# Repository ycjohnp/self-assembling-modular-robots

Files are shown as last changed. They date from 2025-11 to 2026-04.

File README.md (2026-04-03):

# A Fully Automatic Self-Assembling Modular Robot System (Archived)



 This project showcases the design and manufacturing of a self-assembling modular robotic system, with each robot possessing 4 degrees of freedom, wheel-based locomotion, Bluetooth and Wi-Fi capabilities, and an electromagnet-based connection system.

Controlled through a combination of AprilTags, computer vision using OpenCV, and PID controllers for precise position and movement instructions, the system's functionality has been validated through extensive tests. These tests include assessing the robot's speed in various assembly configurations, speed under cargo load, and the strength of inter-robot connections. Simulated challenging environments were created to validate the overall self-assembly performance of the robotic system.

## How This Project Started

During the spring of 2022, Shanghai went into a 3-month long lockdown, due to a major Covid-19 outbreak. During that time we were unable to leave our homes and for many weeks we had a hard time getting supplies and food or getting anything delivered since essential logistics and delivery workers were unable to go to work. 

During that time I started researching: "How can we increase the reliability of logistics and delivery networks?" Many of the ideas that popped up during that initial research mentioned **flexibility** and **adaptability** in the industry and in the subprocess (eg. last-mile delivery, warehousing, transportation, etc.).

Going off of my past robotics experience, I knew that modular robots met the exact characteristics mentioned above. Seeing current modular robotics research focused on search & rescue and static applications of modular robots (such as sending them to Mars before humans to build structures), I wondered: "Can we use robots that solve challenges together to increase reliability and decrease human dependence of logistics systems?”

I began this project to build a self-assembling modular robot system for logistics, though its design can be applied to other use cases as well. Although this is just a proof-of-concept system, I hope the insights from this research can open up possibilities for further industrial applications of modular robotics. By doing so, I hope that this critical part of our daily lives becomes more resilient against extreme situations
## Demo
Modular Robot Demo (http://www.youtube.com/watch?v=8HDp2pXij3Y "Modular Robot Demo")

## Project Pictures





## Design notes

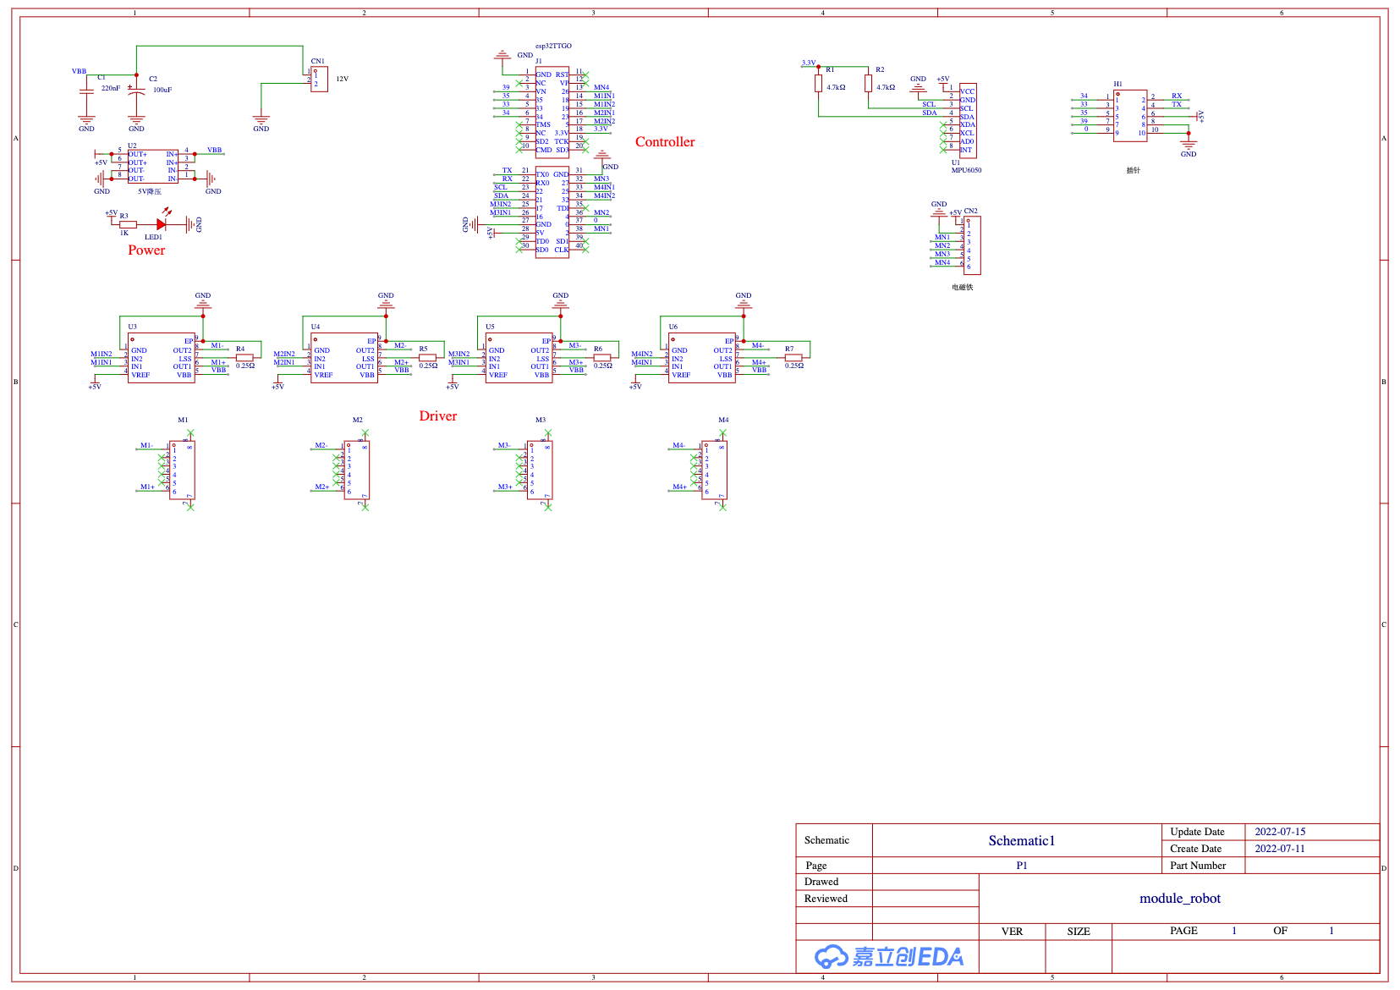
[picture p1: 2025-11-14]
Extension Board PCB/PCB Schematics.png

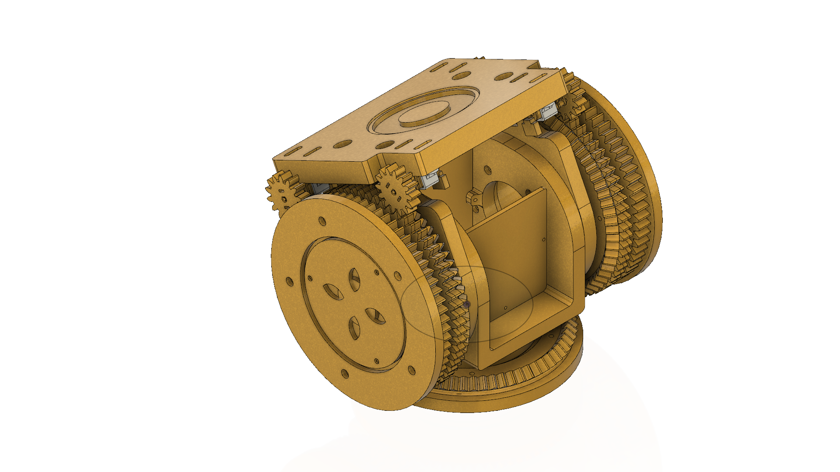
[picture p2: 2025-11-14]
3D Files/Module_robot.png

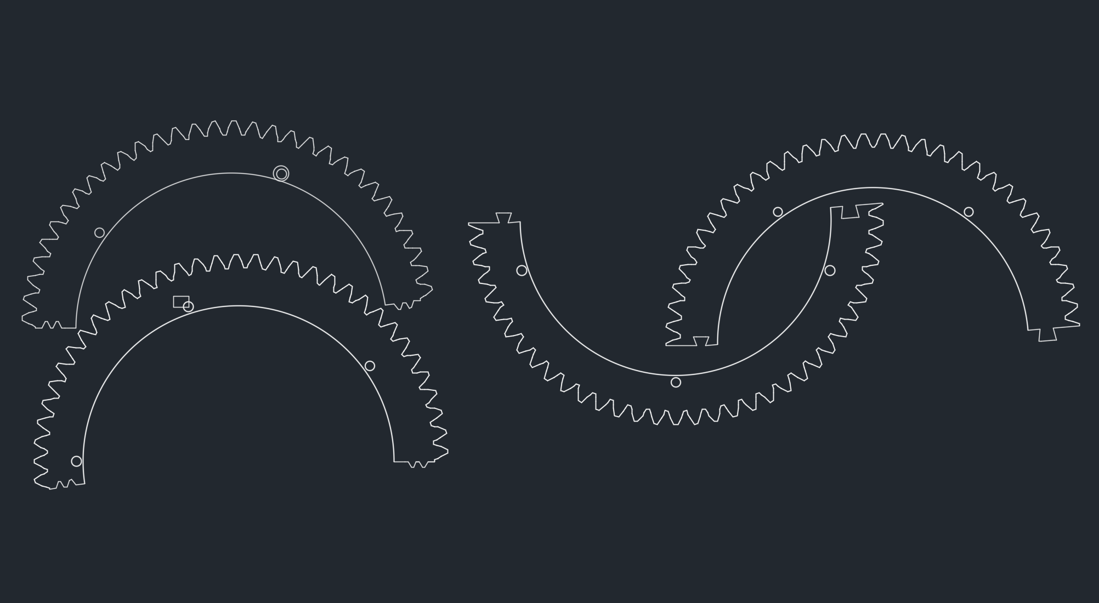
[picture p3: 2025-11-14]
2D DWG/Bevel Gear Halves DWG.png

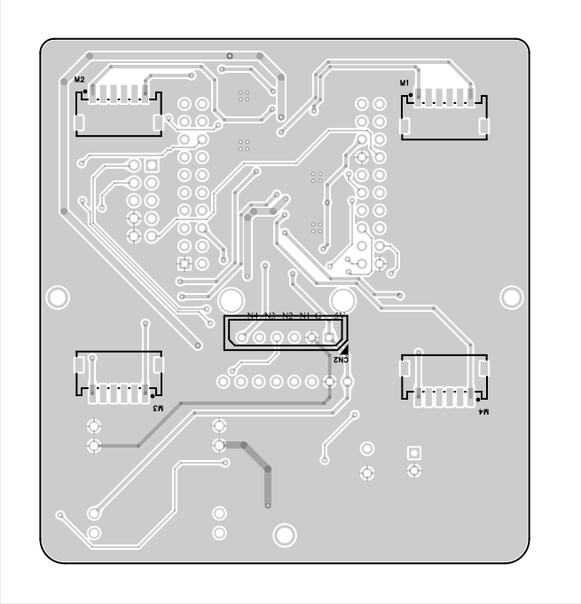
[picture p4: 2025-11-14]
Extension Board PCB/PCB Back.png

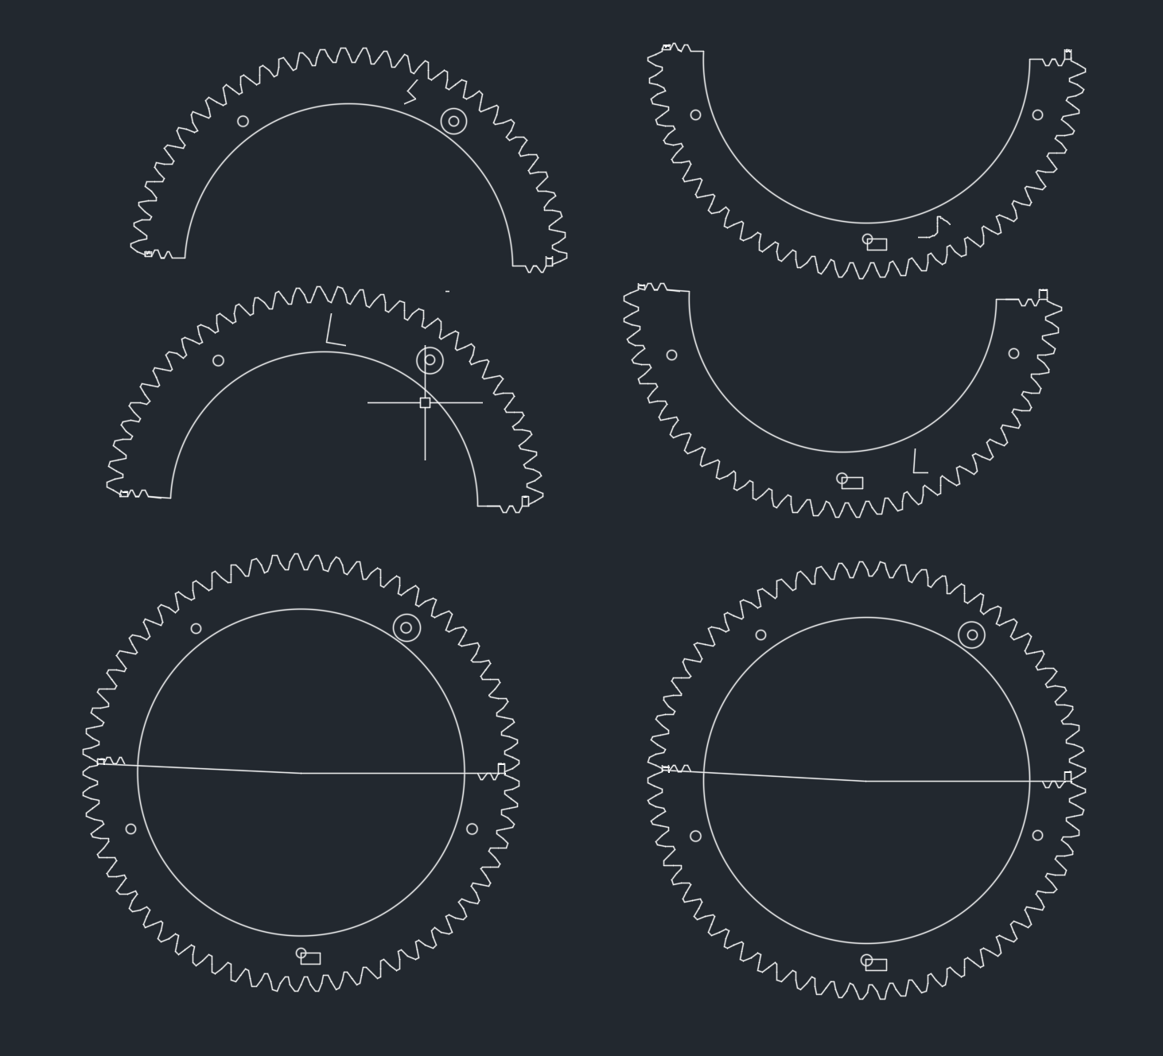
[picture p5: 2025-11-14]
2D DWG/Wheel Gear Halves DWG.png

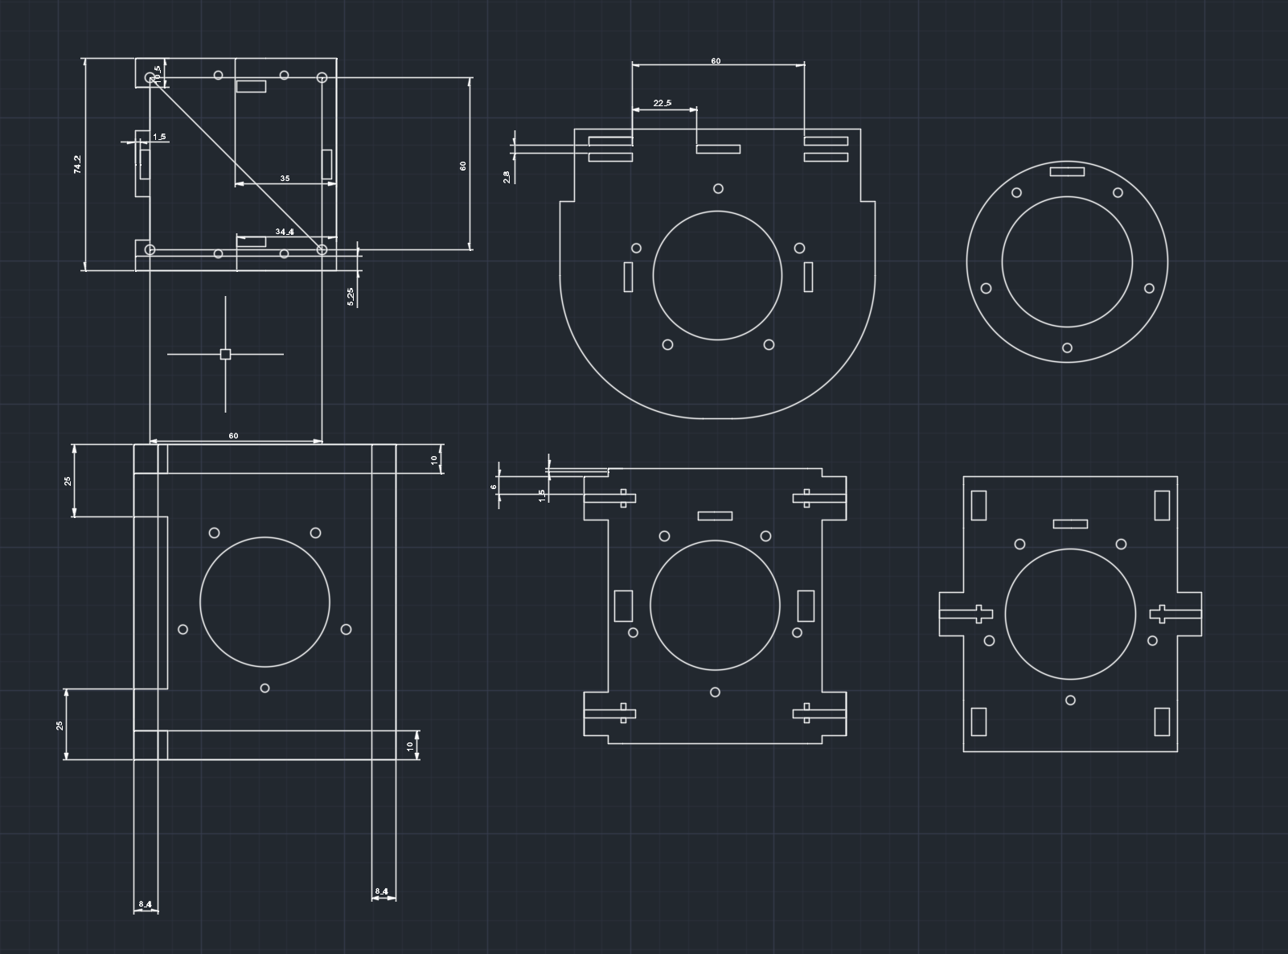
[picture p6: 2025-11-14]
2D DWG/Center Frame DWG.png

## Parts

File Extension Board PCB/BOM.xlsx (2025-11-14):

No. | Quantity | Device | Designator | Footprint | Value | Manufacturer Part | Manufacturer | Supplier Part | Supplier
1 | 1 | TCC0603X5R224M250CT | C1 | C0603 | 220nF | TCC0603X5R224M250CT | CCTC(三环) | C713508 | LCSC
2 | 1 | RG050M101LO8*12TA-1A1E | C2 | CAP-TH_BD8.0-P3.50-D0.6-FD | 100uF | RG050M101LO8*12TA-1A1E | BERYL(绿宝石) | C357618 | LCSC
3 | 1 | HC-5264-2A | CN1 | CONN-TH_2P-P2.50_HCTL_HC-5264-2A |  | HC-5264-2A | HCTL(华灿天禄) | C2845814 | LCSC
4 | 1 | HC-5264-6A | CN2 | CONN-TH_6P-P2.50_HCTL_HC-5264-6A |  | HC-5264-6A | HCTL(华灿天禄) | C2845818 | LCSC
5 | 1 | HDR-M_2.54_2x5 | H1 | HDR-TH_10P-P2.54-V-M-R2-C5-S2.54 |  |  |  | C124387
6 | 1 | esp32ttgo | J1 | esp32TTGO
7 | 1 | LED_0603-R | LED1 | LED0603-RD_BLUE |  |  |  | C72044
8 | 4 | KH-ZH1.5WF-06A | M1,M2,M3,M4 | CONN-SMD_KH-ZH1.5WF-06A |  | KH-ZH1.5WF-06A | kinghelm(金航标) | C2688783 | LCSC
9 | 2 | AR05DTCW1002 | R1,R2 | R0805 | 4.7kΩ | AR05DTCW1002 | 光颉(Viking) | C319941 | LCSC
10 | 1 | Res_0603 | R3 | R0603 | 1K
11 | 4 | CR2512FR250E04R | R4,R5,R6,R7 | R2512 | 0.25Ω | CR2512FR250E04R | EVER OHMS(天二科技) | C147045 | LCSC
12 | 1 | MPU6050 | U1 | MPU6050
13 | 1 | bianyaqi | U2 | bianyaqi
14 | 4 | A4950ELJTR-T | U3,U4,U5,U6 | SOIC-8_L4.9-W3.9-P1.27-LS6.0-BL-EP |  | A4950ELJTR-T | ALLEGRO(美国埃戈罗) | C82404 | LCSC

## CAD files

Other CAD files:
2D DWG/Bevel Gear Halves DWG.dwg
2D DWG/Wheel Gear Halves DWG.dwg
2D DWG/Center Frame DWG.dwg

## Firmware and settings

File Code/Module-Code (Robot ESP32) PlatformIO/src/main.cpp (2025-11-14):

#include <Arduino.h>
#include "ESPMotor.hpp"
#include <MPU6050_tockn.h>
#include <Wire.h>
#include <esp_now.h>
#include <WiFi.h>

typedef struct test_struct
{
  float distance; // x
  float angle;    // y
  float state;    // z
} test_struct;

test_struct myData;

void OnDataRecv(const uint8_t *mac, const uint8_t *incomingData, int len)
{
  memcpy(&myData, incomingData, sizeof(myData));
  // Serial.print("Bytes received: ");
  // Serial.println(len);
  // Serial.print("x: ");
  Serial.print(myData.distance);
  Serial.print(",");
  Serial.print(myData.angle);
  Serial.print(",");
  Serial.print(myData.state);
  Serial.println();
}

// PWM availible on : 2, 4, 5, 12 - 19, 21 - 23, 25 - 27, 32 - 33
//----------------------------------------------------------------
// Motor Pins
#define M1IN1 18
#define M1IN2 19
#define M2IN1 23
#define M2IN2 5
#define M3IN1 16
#define M3IN2 17
#define M4IN1 25
#define M4IN2 32
//----------------------------------------------------------------
// Electromagnet Pins
#define magnet1pin 2
#define magnet2pin 4
#define magnet3pin 27
#define magnet4pin 26

//----------------------------------------------------------------
// Magnet On
//
#define OpenMagnet(magnetpin)      \
  do                               \
  {                                \
    digitalWrite(magnetpin, HIGH); \
  } while (0);

// Magnet Off
#define CloseMagnet(magnetpin)    \
  do                              \
  {                               \
    digitalWrite(magnetpin, LOW); \
  } while (0);

ESPMotor motor1;
ESPMotor motor2;
ESPMotor motor3;
ESPMotor motor4;

void move(int direct, double speed);
void turret(int direct, double speed);

_PID run_pid;
_PID turn_pid;
_PID turret_pid;

_PID final_pid;

float range;

bool Final_flag = 0;
bool PID_flag = 1;

bool Out_flag = false;

unsigned long start_final = 0;
unsigned long end_final = 0;
long time_passed;

MPU6050 mpu6050(Wire); // Creates instance of gyroscope
void TaskBlink(void *pvParameters); // Creates 2nd thread

void setup()
{
  Serial.begin(115200);


  WiFi.mode(WIFI_STA);

  // Initializes espnow
  if (esp_now_init() != ESP_OK)
  {
    Serial.println("Error initializing ESP-NOW");
    return;
  }

  esp_now_register_recv_cb(OnDataRecv);

  pinMode(magnet1pin, OUTPUT); // Set electromagnet pins to output
  pinMode(magnet2pin, OUTPUT); 
  pinMode(magnet3pin, OUTPUT); 
  pinMode(magnet4pin, OUTPUT); 

  digitalWrite(magnet1pin, LOW); // Default off
  digitalWrite(magnet2pin, LOW); 
  digitalWrite(magnet3pin, LOW); 
  digitalWrite(magnet4pin, LOW); 

  motor1.init(M1IN1, M1IN2);
  motor2.init(M2IN1, M2IN2);
  motor3.init(M3IN1, M3IN2);
  motor4.init(M4IN1, M4IN2);

  turn_pid.Kp = -0.02;
  turn_pid.Kd = 0.04;

  run_pid.Kp = -0.005;
  run_pid.Kd = 0.01;

  final_pid.Kp = -0.015;
  final_pid.Kd = 0.04;

  turret_pid.Kp = 0.028;

  turret_pid.set_pid_target(2.50); // Starting position of Turret

  Wire.begin(21, 22, 400000U);
  mpu6050.begin();
  mpu6050.calcGyroOffsets(true);

  xTaskCreatePinnedToCore(
      TaskBlink, "TaskBlink" 
      ,
      2048 
      ,
      NULL, 1 
      ,
      NULL, ARDUINO_RUNNING_CORE);

}

void loop()
{
  float Keter;

  float turn_speed;
  float middle_speed;
  float final_speed;

  if (myData.state == 3.0 || myData.state == 4.0)
  {
    OpenMagnet(magnet2pin);

    if (myData.state == 4.0)
    {
      turret_pid.set_pid_target(10.0); // lifts turret: 10deg above horizontal
    }
  }
  else if (myData.state == 5.0)
  {
    CloseMagnet(magnet2pin);
    delay(1000);
    if (Out_flag == false)
    {
      move(1, 0.5);
      delay(1000);
      move(1, 0.0);
      turret_pid.set_pid_target(2.50); 
      Out_flag = true;                 
    }
  }

  else
  {
    CloseMagnet(magnet2pin);
  }

  if (myData.distance > 30)
  {
    PID_flag = 1;
  }
  else if (myData.distance < 30)
  {
    PID_flag = 0;
    motor4.run(0);
    motor3.run(0);
  }

  if (PID_flag) // PID_flag
  {
    if (!Final_flag)
    {
      turn_speed = turn_pid.PID_realize(myData.angle);
      middle_speed = run_pid.PID_realize(myData.distance);

      range = abs(myData.angle);

      if (range >= 90)
      {
        motor4.run(middle_speed * 0.05 + turn_speed * 1.5);
        motor3.run(-(middle_speed)*0.05 + turn_speed * 1.5);
      }

      if (range >= 50 && range < 90)
      {
        motor4.run(middle_speed * 0.1 + turn_speed * 1.2);
        motor3.run(-(middle_speed)*0.1 + turn_speed * 1.2);
      }
      if (range >= 24 && range < 50)
      {
        motor4.run(middle_speed * 0.2 + turn_speed);
        motor3.run(-(middle_speed)*0.2 + turn_speed);
      }
      if (range >= 8 && range < 24)
      {
        motor4.run(middle_speed * 0.4 + turn_speed);
        motor3.run(-(middle_speed)*0.4 + turn_speed);
      }
      if (range >= 2 && range < 8)
      {
        motor4.run(middle_speed * 0.8 + turn_speed);
        motor3.run(-(middle_speed)*0.8 + turn_speed);
      }
      if (range >= 0 && range < 2)
      {
        motor4.run(middle_speed * 1 + turn_speed);
        motor3.run(-(middle_speed)*1 + turn_speed);
      }
    }
  }
  else
  {
  }
}

void TaskBlink(void *pvParameters) 
{
  (void)pvParameters;

  for (;;) 
  {
    delay(20);
    mpu6050.update();
    float turret_speed = turret_pid.PID_realize(mpu6050.getAngleY());
    motor1.run(turret_speed);
    motor2.run(turret_speed);
    unsigned int stackLeft = uxTaskGetStackHighWaterMark(NULL);
  }
}

// 1 forward, 2 right, 3 backward, 4 left//
void move(int direct, double speed)
{
  switch (direct)
  {
  case 1: 
    motor3.run(speed);
    motor4.run(-(speed));
    break;
  case 2:
    motor3.run(speed);
    motor4.run(speed);
    break;
  case 3:
    motor3.run(-(speed));
    motor4.run(speed);
    break;
  case 4:
    motor3.run(-(speed));
    motor4.run(-(speed));
    break;
  default:
    break;
  }
}

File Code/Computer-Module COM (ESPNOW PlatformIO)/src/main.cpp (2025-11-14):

#include <esp_now.h>
#include <WiFi.h>
#include <Arduino.h>

float Parameter[4];
String packet = "";

// robots id and their corresponding mac address
uint8_t broadcastAddress1[] = {0x94, 0xB5, 0x55, 0xC8, 0xCC, 0x8C}; // robot 1
uint8_t broadcastAddress2[] = {0x94, 0xB5, 0x55, 0xC8, 0xCC, 0x48}; // robot 2
uint8_t broadcastAddress3[] = {0x94, 0xB5, 0x55, 0xC8, 0xD5, 0x14}; // robot 3

typedef struct test_struct {
  float distance;
  float angle;
  float state;
} test_struct;


  test_struct robotdata;


void OnDataSent(const uint8_t *mac_addr, esp_now_send_status_t status) {
  char macStr[18];
  Serial.print("Packet to: ");
  // Copies the sender mac address to a string
  snprintf(macStr, sizeof(macStr), "%02x:%02x:%02x:%02x:%02x:%02x",
           mac_addr[0], mac_addr[1], mac_addr[2], mac_addr[3], mac_addr[4], mac_addr[5]);
  Serial.print(macStr);
  Serial.print(" send status:\t");
  Serial.println(status == ESP_NOW_SEND_SUCCESS ? "Delivery Success" : "Delivery Fail");
}

// Decodes the incoming transmission in format: "(tag-id),(distance to target,(angle to target),(robot state)/" //
// Sample transmission: "3,200.89,56.98,1/" //

void Decode() {
  String Temp = "";
  if (packet.length() > 0) {  /* incoming packet from serial port containing id, distance, and angle data */
    int j = 0;
    for (int i = 0; i < packet.length() ; i++) {
      if (packet[i] == ',') {    // "," as seperator between values
        Parameter[j] = Temp.toFloat();   // converts string to float
        Temp = "";                 // clear temp to for next value
        j++;
      }
      else if (packet[i] == '/') {    // end of packet indicator  
        Parameter[j] = Temp.toFloat();
        Temp = "";
        j = 0;
      }
      else {
        Temp += packet[i];
      }
    }
  }
}

void setup() {

  Serial.begin(115200);

  WiFi.mode(WIFI_STA);

  if (esp_now_init() != ESP_OK) {
    Serial.println("Error initializing ESP-NOW");
    return;
  }

  esp_now_register_send_cb(OnDataSent);

  // register peer
  esp_now_peer_info_t peerInfo;
  peerInfo.channel = 0;
  peerInfo.encrypt = false;

  memcpy(peerInfo.peer_addr, broadcastAddress1, 6);
  if (esp_now_add_peer(&peerInfo) != ESP_OK) {
    Serial.println("Failed to add peer");
    return;
  }

  memcpy(peerInfo.peer_addr, broadcastAddress2, 6);
  if (esp_now_add_peer(&peerInfo) != ESP_OK) {
    Serial.println("Failed to add peer");
    return;
  }
  memcpy(peerInfo.peer_addr, broadcastAddress3, 6);
  if (esp_now_add_peer(&peerInfo) != ESP_OK) {
    Serial.println("Failed to add peer");
    return;
  }

  

}

void loop() {

  if (Serial.available()) {
    delay(2);

    while (Serial.available()) {
      packet += char(Serial.read());

    }
    Decode();

    robotdata.distance = Parameter[1];
    robotdata.angle = Parameter[2];
    robotdata.state = Parameter[3];

  if (Parameter[0] == 1.0) {
    esp_err_t result1 = esp_now_send(
                          broadcastAddress1,
                          (uint8_t *) &robotdata,
                          sizeof(test_struct));
  }

  else if (Parameter[0] == 2.0) {
    esp_err_t result2 = esp_now_send(
                          broadcastAddress2,
                          (uint8_t *) &robotdata,
                          sizeof(test_struct));


  }

  else if (Parameter[0] == 3.0) {
    esp_err_t result3 = esp_now_send(
                          broadcastAddress3,
                          (uint8_t *) &robotdata,
                          sizeof(test_struct));
  }

  }


}
